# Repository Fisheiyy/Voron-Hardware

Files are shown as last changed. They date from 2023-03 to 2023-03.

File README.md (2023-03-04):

# Voron-Hardware
Cool Hardware designed by the Voron Design group

| Project | Overview |
|---|---|
| Afterburner_Toolhead_PCB | Breakout PCB for the Afterburner toolhead |
| Daylight on a Stick | LED PCB to illuminate your printer |
| Hall_Effect_XY_Endstop | Replacement for mechanical endstop switches with an adjustable magnetic endstop PCB |
| Klipper_Expander | Standalone MCU for use with Klipper with various inputs and outputs |
| Microswitch_Endstop | PCB for mechanical endstop switches |
| Microswitch_Z_Endstop | PCB for mechanical Z endstop switches |
| Nano_Display | Adapts an Arduino Nano to the RepRap standard 2 2x5pin IDC Connectors |
| PT100Stick | PT100 board in StepStick format |
| SKR-Mini_Screen_Adaptor | PCB to connect a 2 2x5 IDC cable screen to an SKR Mini E3 V1.2/2.0 |
| STM32_Mini12864 | A standalone MCU for use with Klipper to drive a FYSETC Mini 12864 Display |
| Stealthburner_Toolhead_PCB | Breakout PCB for the Afterburner toolhead |
| Taco_Raven | 3D Printer controller with 8 integrated stepper drivers for use with Klipper |
| V0-Umbilical | Set of two PCBs for use with the V0.1 to make wiring easier and more modular |
| V0_Display | Small Form Factor Display with OLED, Rotary Encoder or Buttons and Neopixel LED |
| V0_Display_RP2040	 | Derivitive of V0 Display to use RP2040 over STM32 |
| V0_Micro_Display | Micro Form Factor Display with OLED, Clickable D-pad and Neopixel LED |
| V0_PCB_Mod | V0 Mod by JNP |
| V0_Simple_Display | V0 Simple Display is a remix of the V0 Display that doesnt need an STM32 MCU |

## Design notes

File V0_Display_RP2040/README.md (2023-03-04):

# RP2040 V0 Display #
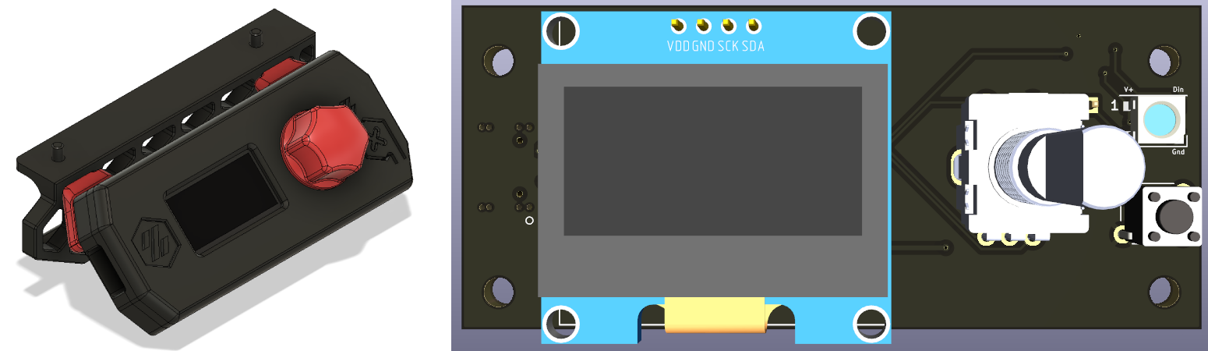
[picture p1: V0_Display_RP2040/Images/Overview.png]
V-Naught_Display


[iBOM](http://htmlpreview.github.io/?https://github.com/Fisheiyy/RP2040_V0_Display/blob/master/KiCad/ibom.html)
### Derived from [Timmit99's V0 Display](https://github.com/VoronDesign/Voron-Hardware/tree/master/V0_Display)
### Sponsored by Provok3d.com & Lab4450.com

## The board has: ##
 - RP2040 MCU with 12MHz Crystal
 - SWD header for easy debugging (not populated by default)
 - USB C port
 - I2C Screen connections for  1.3" display with jumpers on back for slecting which pins (1 or 2) are power and ground
 - EN11-style click encoder support
 - Reset/kill button
 - 3 GPIO pin header
 - 1 on-board Neopixel with data line broken out for expansion

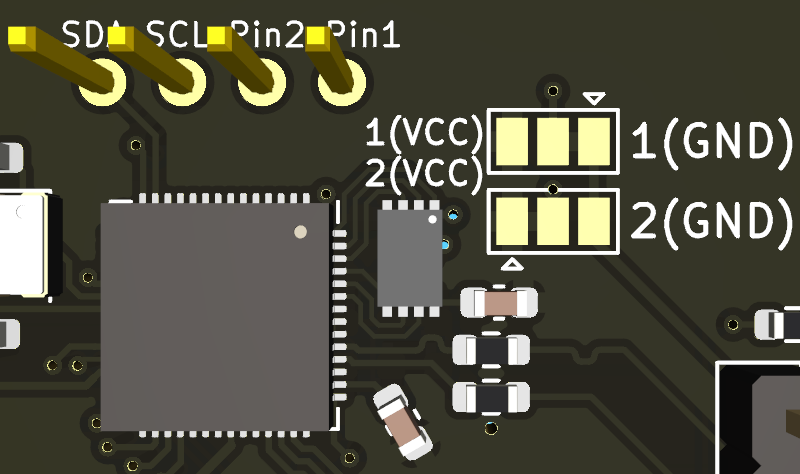
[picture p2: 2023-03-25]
V0_Display_RP2040/Images/I2C_Power_Pin_Selection.PNG

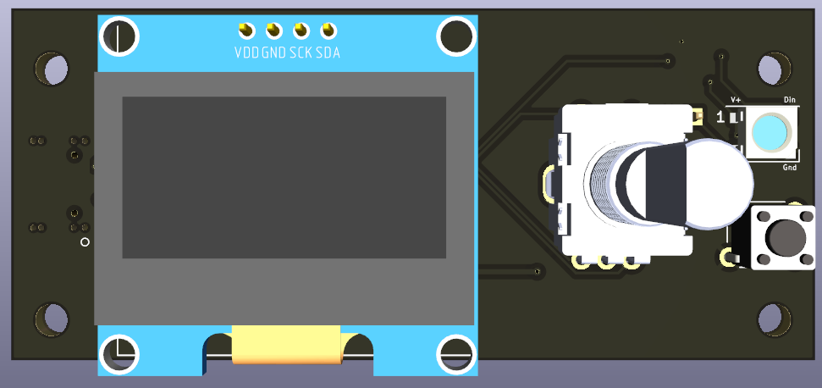
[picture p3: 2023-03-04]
V0_Display_RP2040/Images/Front.png

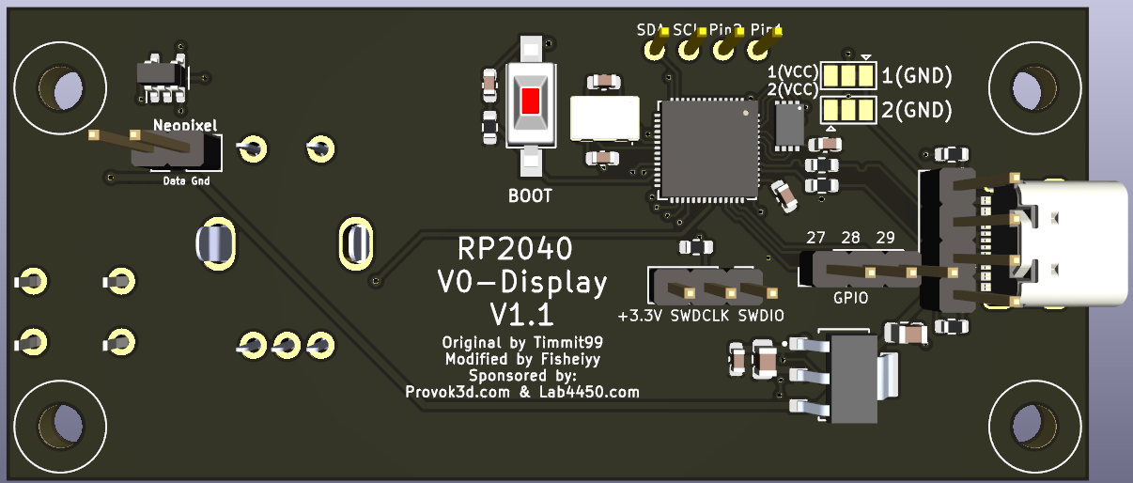
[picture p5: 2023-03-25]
V0_Display_RP2040/Images/Rear.png

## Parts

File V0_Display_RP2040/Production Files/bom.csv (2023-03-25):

Designator | Footprint | Quantity | Value | LCSC Part #
C1, C3 | 0805 | 2 | 22uF | C2859526
C10, C11, C7 | 0603 | 3 | 2.2uF | C71000
C12, C13, C14, C2, C4, C6, C8, C9 | 0603 | 8 | 0.1uF | C30926
C15, C5 | 0603 | 2 | 12pF | C107034
D1 | LED_WS2812B_PLCC4_5.0x5.0mm_P3.2mm | 1 | WS2812B | C2843785
H1, H2, H3, H4 | MountingHole_3.2mm_M3 | 4 | MountingHole
J1 | PinHeader_1x03_P2.54mm_Vertical | 1 | GPIO | C429954
J2 | 1pt3in_OLED | 1 | I2C Header | N/A
J3 | PinHeader_1x03_P2.54mm_Vertical | 1 | SWD | C429954
J4 | USB_C_Receptacle_G-Switch_GT-USB-7010ASV | 1 | GT-USB-7010ASV | C2988369
J5 | PinHeader_1x04_P2.54mm_Vertical | 1 | USB_Header
J6 | PinHeader_1x02_P2.54mm_Vertical | 1 | Neopixel | C2894925
JP1 | SolderJumper-3_P1.3mm_Bridged12_Pad1.0x1.5mm | 1 | Pin2 | N/A
JP2 | SolderJumper-3_P1.3mm_Bridged12_Pad1.0x1.5mm | 1 | Pin1 | N/A
JP3 | SW_SPST_FSMSM | 1 | RUN | C118141
R1, R3, R6, R8 | 0603 | 4 | 10K | C304415
R2 | 0603 | 1 | 1K | C110774
R4, R5 | 0603 | 2 | 27R | C861276
R7 | 0603 | 1 | 200R | C8218
SW1 | SW_PUSH_6mm | 1 | Kill_SW | C455090
SW2 | EN11_Encoder | 1 | Rotary_Enc | N/A
U1 | AMS1117-3.3 | 1 | AMS1117-3.3 | C6186
U2 | W25Q16JVUXIQ | 1 | W25Q16JVUXIQ | C2843335
U3 | SOT-23-5 | 1 | 74LVC1G17 | C6076
U4 | QFN-56-1EP_7x7mm_P0.4mm_EP3.2x3.2mm | 1 | RP2040 | C2040
Y1 | Oscillator_SMD_SeikoEpson_SG8002CE-4Pin_3.2x2.5mm | 1 | 12MHz | C654949

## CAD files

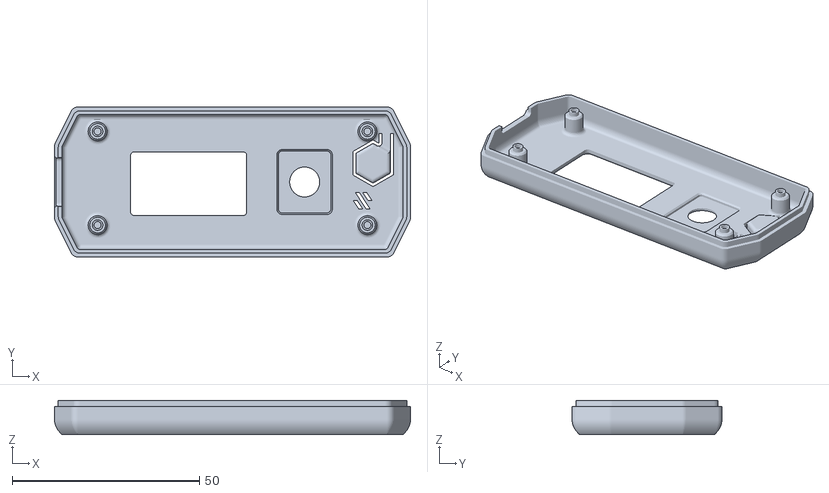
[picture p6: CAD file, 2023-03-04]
V0_Display_RP2040/STLs/Housing_Front_x1.stl
95.0 x 40.0 x 9.10

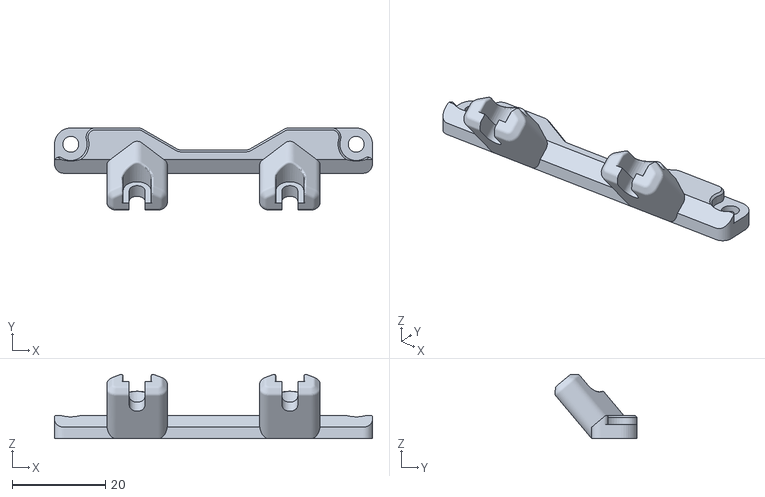
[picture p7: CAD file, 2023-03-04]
V0_Display_RP2040/STLs/V0.1/[a]SinglePieceMount_Slot_x1.STL
68.3 x 17.6 x 13.8

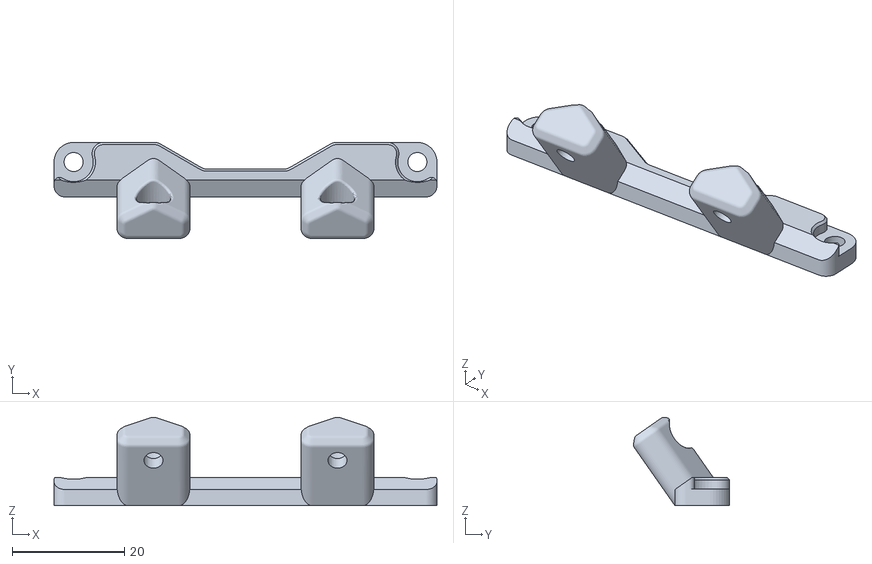
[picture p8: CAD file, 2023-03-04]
V0_Display_RP2040/STLs/V0.1/[a]_Single_Piece_Mount_x1.STL
68.3 x 17.1 x 15.8

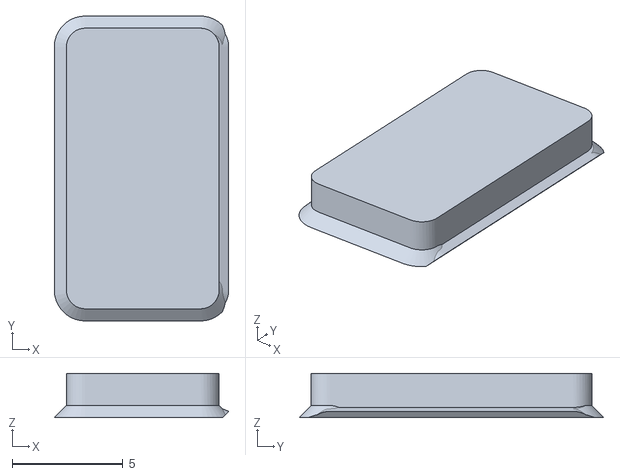
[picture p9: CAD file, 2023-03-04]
V0_Display_RP2040/STLs/USB_Opening_Plug_x1.STL
7.89 x 13.8 x 2.00

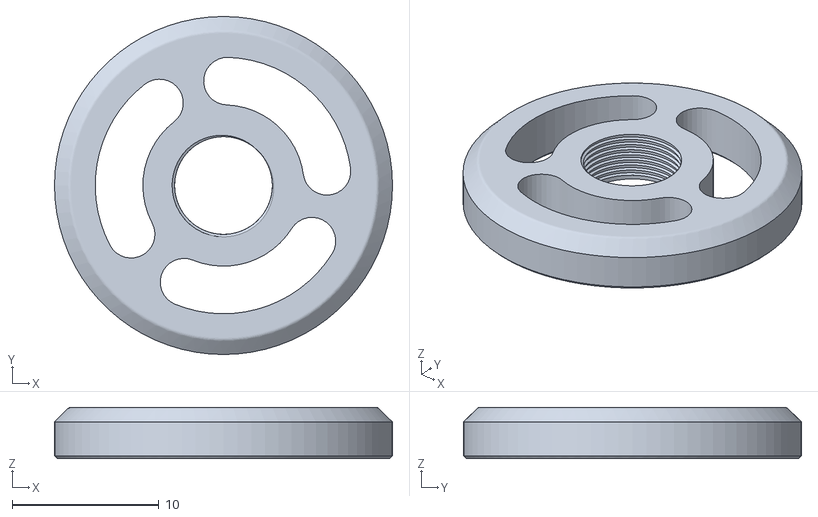
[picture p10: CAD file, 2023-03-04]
V0_Display_RP2040/STLs/[a]_Knob_Spacer_x1.stl
23.0 x 23.0 x 3.50

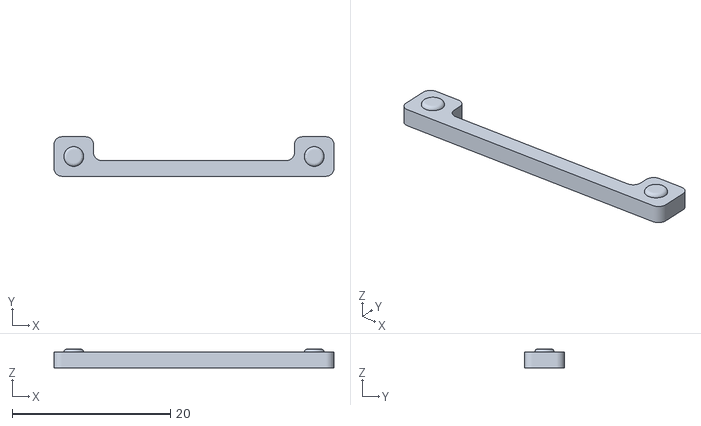
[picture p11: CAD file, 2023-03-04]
V0_Display_RP2040/STLs/Screen_Spacer_x1.stl
35.4 x 5.00 x 2.40

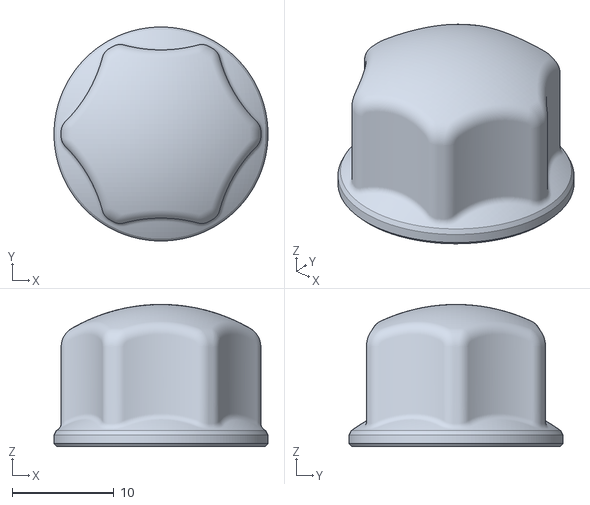
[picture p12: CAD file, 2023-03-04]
V0_Display_RP2040/STLs/[a]_Knob_x1.stl
21.0 x 21.0 x 13.9

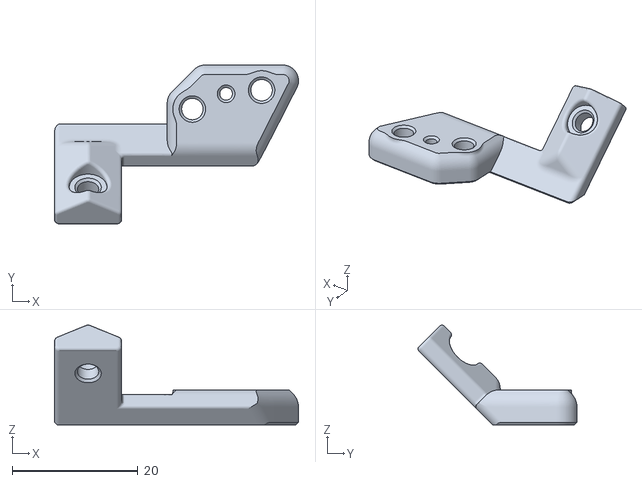
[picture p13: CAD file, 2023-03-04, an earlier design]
V0_Display_RP2040/STLs/V0/[a]_Mounting_leg_x1.stl
38.8 x 25.3 x 15.9

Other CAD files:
V0_Display_RP2040/STLs/Housing_Front_No_USB_x1.stl
V0_Display_RP2040/STLs/V0/[a]_Mounting_leg_mirror_x1.stl

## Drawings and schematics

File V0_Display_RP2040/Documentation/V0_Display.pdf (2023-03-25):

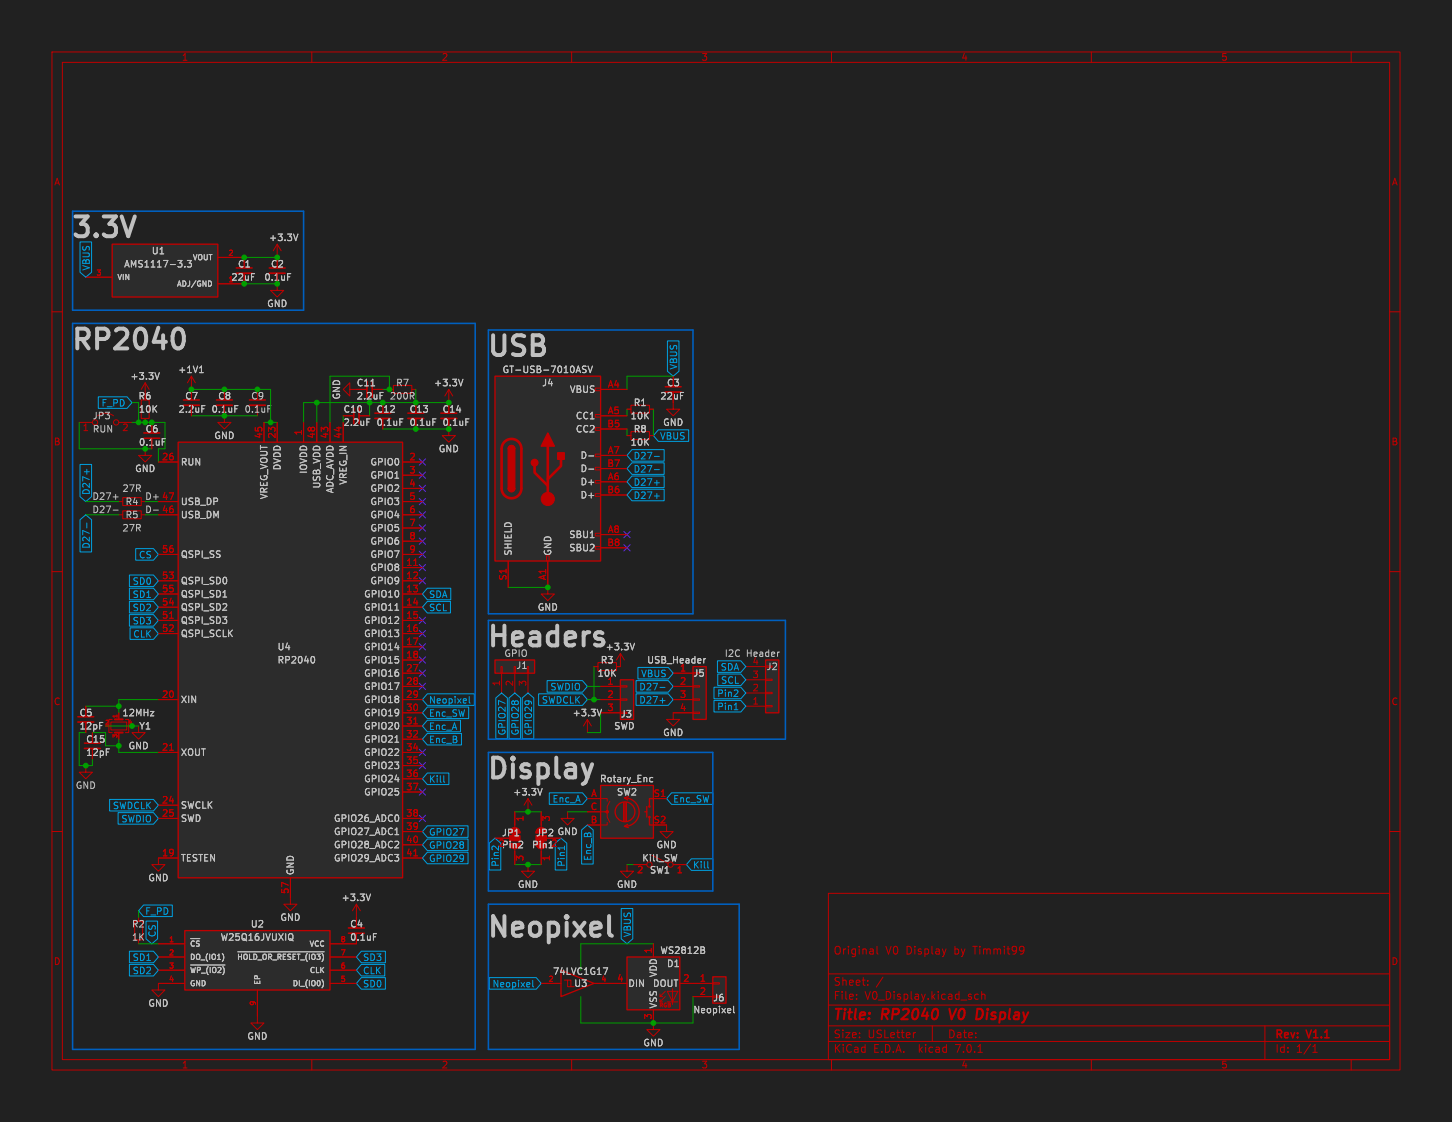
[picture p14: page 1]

D1 WS2812B VDD 1 DOUT 2 VSS 3 DIN 4

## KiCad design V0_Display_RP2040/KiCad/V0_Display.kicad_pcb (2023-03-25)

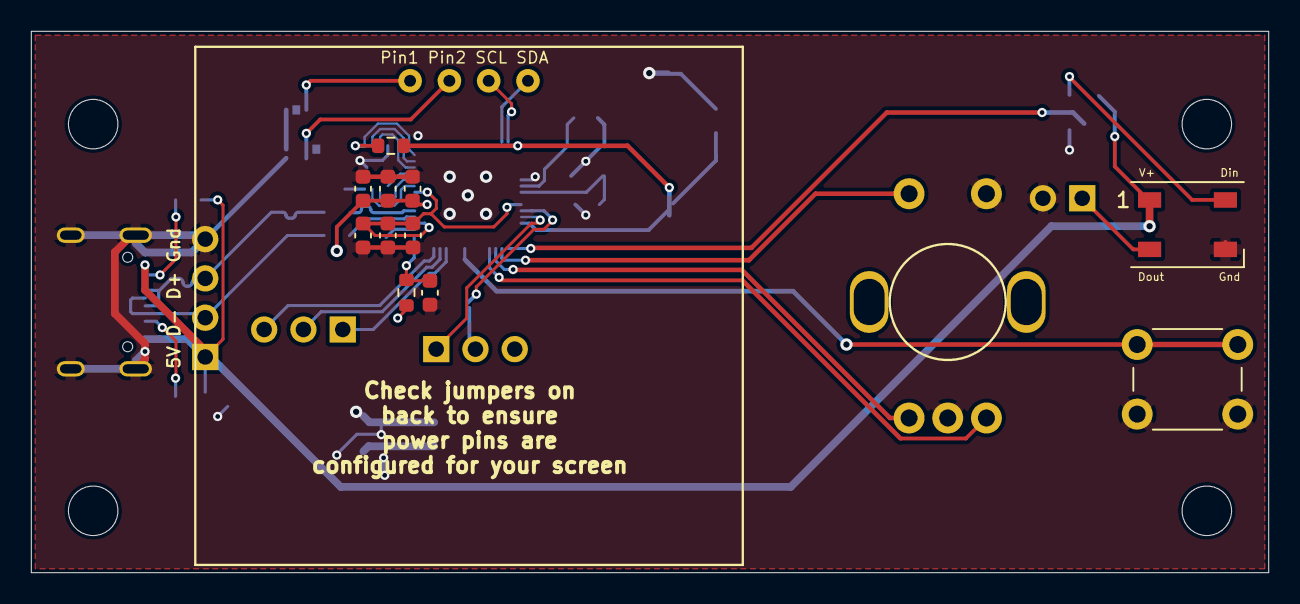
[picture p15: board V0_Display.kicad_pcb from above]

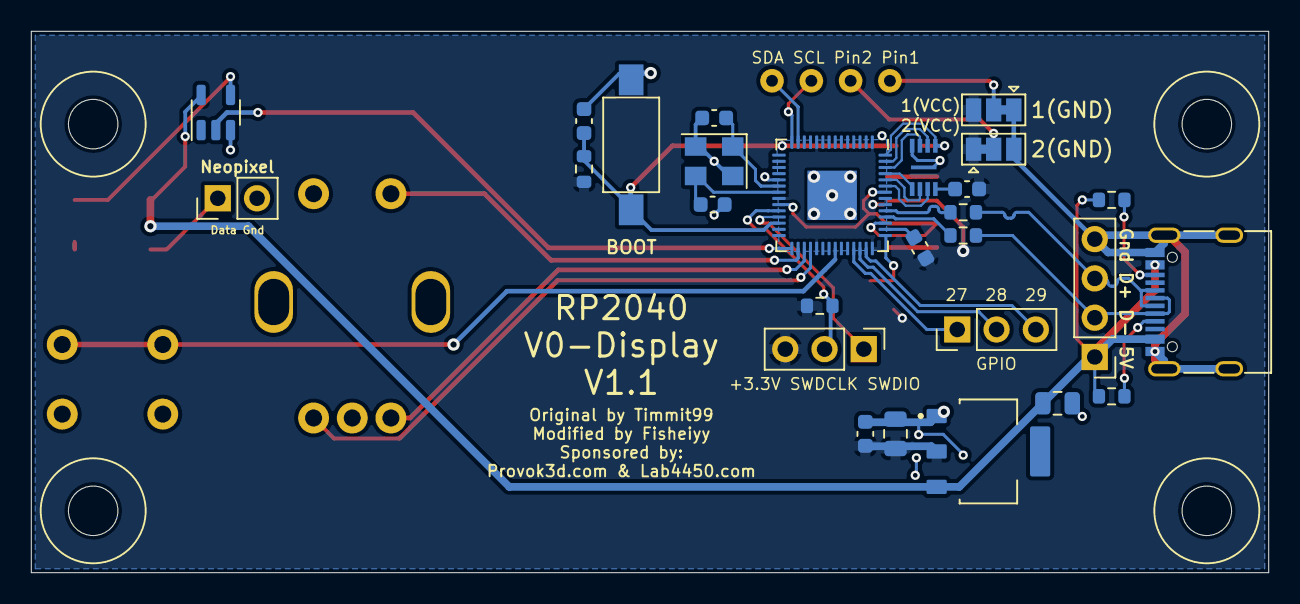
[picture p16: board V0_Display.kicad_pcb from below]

Board: 2 copper layers, 80.0 x 35.0 mm, 44 parts (27 on the bottom side), 38 nets.

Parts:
C1, C3: 22uF; C_0805_2012Metric
C2, C4, C6, C8, C9, C12, C13, C14: 0.1uF; C_0603_1608Metric
C5, C15: 12pF; C_0603_1608Metric
C7, C10, C11: 2.2uF; C_0603_1608Metric
D1: WS2812B; LED_WS2812B_PLCC4_5.0x5.0mm_P3.2mm
H1, H2, H3, H4: MountingHole; MountingHole_3.2mm_M3
J1: GPIO; PinHeader_1x03_P2.54mm_Vertical
J2: I2C Header; 1pt3in_OLED
J3: SWD; PinHeader_1x03_P2.54mm_Vertical
J4: GT-USB-7010ASV; USB_C_Receptacle_G-Switch_GT-USB-7010ASV
J5: USB_Header; PinHeader_1x04_P2.54mm_Vertical
J6: Neopixel; PinHeader_1x02_P2.54mm_Vertical
JP1: Pin2; SolderJumper-3_P1.3mm_Bridged12_Pad1.0x1.5mm
JP2: Pin1; SolderJumper-3_P1.3mm_Bridged12_Pad1.0x1.5mm
JP3: RUN; SW_SPST_FSMSM
R1, R3, R6, R8: 10K; R_0603_1608Metric
R2: 1K; R_0603_1608Metric
R4, R5: 27R; R_0603_1608Metric
R7: 200R; R_0603_1608Metric
SW1: Kill_SW; SW_PUSH_6mm
SW2: Rotary_Enc; EN11_Encoder
U1: AMS1117-3.3
U2: W25Q16JVUXIQ
U3: 74LVC1G17; SOT-23-5
U4: RP2040; QFN-56-1EP_7x7mm_P0.4mm_EP3.2x3.2mm
Y1: 12MHz; Oscillator_SMD_SeikoEpson_SG8002CE-4Pin_3.2x2.5mm

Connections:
+1V1: C7.1, C8.1, C9.1, U4.23 (DVDD), U4.45 (VREG_VOUT), U4.50 (DVDD)
+3.3V: C1.1, C2.1, C4.2, C10.1, C12.1, C13.1, C14.1, J3.3, JP1.1 (A), JP2.3 (B), R3.2, R6.2, R7.2, U1.2 (VOUT), U4.1 (IOVDD), U4.10 (IOVDD), U4.22 (IOVDD), U4.33 (IOVDD), U4.42 (IOVDD), U4.48 (USB_VDD), U4.49 (IOVDD)
/D+: R4.2, U4.47 (USB_DP)
/D-: R5.1, U4.46 (USB_DM)
CLK: U2.6 (CLK), U4.52 (QSPI_SCLK)
CS: R2.1, U2.1 (~CS), U4.56 (QSPI_SS)
D27+: J4.A6 (D+), J4.B6 (D+), J5.3, R4.1
D27-: J4.A7 (D-), J4.B7 (D-), J5.2, R5.2
Enc_A: SW2.A, U4.31 (GPIO20)
Enc_B: SW2.B, U4.32 (GPIO21)
Enc_SW: SW2.S1, U4.30 (GPIO19)
F_PD: C6.2, JP3.2 (B), R2.2, R6.1, U4.26 (RUN)
GND: C1.2, C2.2, C3.2, C5.2, C6.1, C7.2, C8.2, C9.2, C11.2, C12.2, C13.2, C14.2, C15.2, D1.3 (VSS), J4.A1 (GND), J4.A12 (GND), J4.B1 (GND), J4.B12 (GND), J4.S1 (SHIELD), J5.4, J6.2, JP1.3 (B), JP2.1 (A), JP3.1 (A), SW1.2 (B), SW2.C, SW2.S2, U1.1 (ADJ/GND), U2.4 (GND), U2.9 (EP), U3.3 (GND), U4.19 (TESTEN), U4.57 (GND), Y1.2, Y1.4
GPIO27: J1.1, U4.39 (GPIO27_ADC1)
GPIO28: J1.2, U4.40 (GPIO28_ADC2)
GPIO29: J1.3, U4.41 (GPIO29_ADC3)
Kill: SW1.1 (A), U4.36 (GPIO24)
Neopixel: U3.2, U4.29 (GPIO18)
unnamed: D1.4 (DIN), U3.4
unnamed: D1.2 (DOUT), J6.1
unnamed: J4.A5 (CC1), R1.1
unnamed: J4.B5 (CC2), R8.1
unnamed: C4.1, U2.8 (VCC)
unnamed: C11.1, R7.1, U4.43 (ADC_AVDD)
unnamed: C10.2, U4.44 (VREG_IN)
unnamed: C5.1, U4.20 (XIN), Y1.1
unnamed: C15.1, U4.21 (XOUT), Y1.3
Pin1: J2.1, JP2.2 (C)
Pin2: J2.2, JP1.2 (C)
SCL: J2.3, U4.14 (GPIO11)
SD0: U2.5 (DI_(IO0)), U4.53 (QSPI_SD0)
SD1: U2.2 (DO_(IO1)), U4.55 (QSPI_SD1)
SD2: U2.3 (~WP_(IO2)), U4.54 (QSPI_SD2)
SD3: U2.7 (~HOLD_OR_RESET_(IO3)), U4.51 (QSPI_SD3)
SDA: J2.4, U4.13 (GPIO10)
SWDCLK: J3.2, R3.1, U4.24 (SWCLK)
SWDIO: J3.1, U4.25 (SWD)
VBUS: C3.1, D1.1 (VDD), J4.A4 (VBUS), J4.A9 (VBUS), J4.B4 (VBUS), J4.B9 (VBUS), J5.1, R1.2, R8.2, U1.3 (VIN), U3.5 (VCC)

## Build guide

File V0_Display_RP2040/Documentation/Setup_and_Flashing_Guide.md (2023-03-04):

## V0 Display Flashing Instructions:

1) Connect to your host raspberry pi via SSH

2) This step depends on if your board has firmware on it or not already:

	a) If you have a pre-flashed board:
		- Connect the board to the host Raspberry Pi via USB
		- Jump to step 9
	
	b) If you have an unflashed board:
		- Hold the BOOT button **while** connecting to your Pi via USB

3) Run `lsusb` from the command prompt
	- Make sure you see a `Raspberry Pi RP2 Boot`
	
4) Run `cd ~/klipper` from the command line to enter the Klipper directory

5) Run `make menuconfig` settings should be:

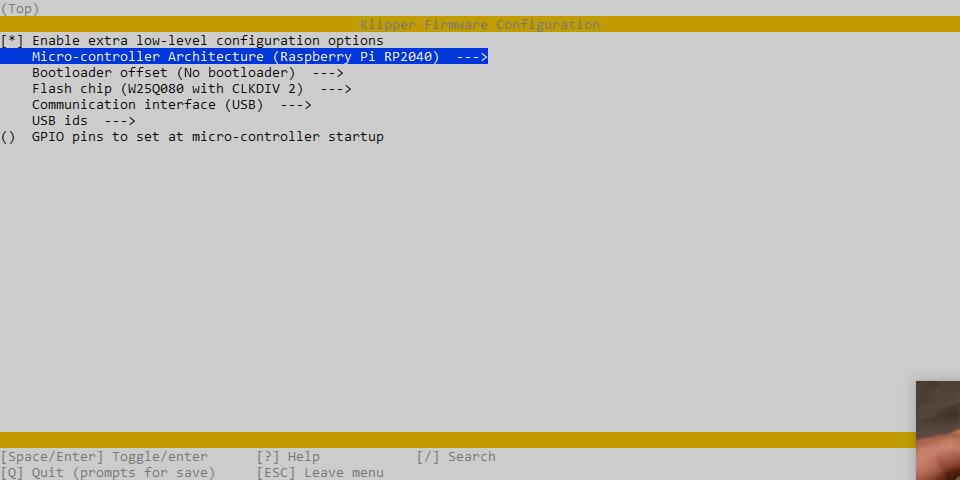
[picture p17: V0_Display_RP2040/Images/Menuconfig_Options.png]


	Exit and Save

6) Run `make clean` to clean up the make environment.

7) Run `make flash FLASH_DEVICE=2e8a:0003`

8) Remove the BOOT jumper

9) Now `ls /dev/serial/by-id/*` should return a device begining with `/dev/serial/by-id/usb-Klipper_rp2040...` 

10) Copy this serial port name (`/dev/serial/by-id/usb-Klipper_rp2040...` )and place it in your [mcu display] section of the display config file.

Your board should now be usable with Klipper. Use the example config file to get started
Best option is to copy the config file into the same directory as `printer.cfg` then add `[include V0Display.cfg]` to the end of your `printer.cfg` to include the file.

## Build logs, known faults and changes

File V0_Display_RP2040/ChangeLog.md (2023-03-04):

# Change Log #

## V1:
 - Changed STM32F042 for RP2040
 - Changed SMD Components from 0805 to 0605
 - Changed USB Micro B to USB C
 - Cleaned up Schematic
 - 1 Ground and 1 3.3V Plane

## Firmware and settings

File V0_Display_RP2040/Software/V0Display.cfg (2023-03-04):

[mcu display]
#serial: **PASTE YOUR SERIAL PORT HERE AND UNCOMMENT**
restart_method: command

[display]
lcd_type: sh1106
i2c_mcu: display
i2c_bus: i2c1
# Set the direction of the encoder wheel
#   Standard: Right (clockwise) scrolls down or increases values. Left (counter-clockwise scrolls up or decreases values.
encoder_pins: ^display:gpio5, ^display:gpio6
#   Reversed: Right (clockwise) scrolls up or decreases values. Left (counter-clockwise scrolls down or increases values.
#encoder_pins: ^display:gpio6, ^display:gpio5
click_pin: ^!display:gpio7
kill_pin: ^!display:gpio8
#x_offset: 2
#   Use X offset to shift the display towards the right. Value can be 0 to 3
#vcomh: 0
#   Set the Vcomh value on SSD1306/SH1106 displays. This value is
#   associated with a "smearing" effect on some OLED displays. The
#   value may range from 0 to 63. Default is 0.
#   Adjust this value if you get some vertical stripes on your display. (31 seems to be a good value)

[neopixel displayStatus]
pin: display:gpio9
chain_count: 1
color_order: GRB
initial_RED: 0.2
initial_GREEN: 0.05
initial_BLUE: 0

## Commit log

2023-03-04 Add V0_Display_RP2040
    [Housing_Front_No_USB_x1.stl, Housing_Front_x1.stl, Screen_Spacer_x1.stl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]
2023-03-05 Fix Footprints
    [V0_Display-B_Cu.gbr, V0_Display-B_Mask.gbr, V0_Display-B_Paste.gbr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]
2023-03-22 Update Files
    New 3.3V Regulator
    "Fixed" Neopixel Level Shifter
    [V0_Display-B_Cu.gbr, V0_Display-B_Mask.gbr, V0_Display-B_Paste.gbr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]
2023-03-25 Rev 1.1
    Fix Vreg-Out Problem
    Change to AMS1117-3.3
    22uF Input Capacitor on VBUS (5V IN)
    [V0_Display-B_Cu.gbr, V0_Display-B_Mask.gbr, V0_Display-B_Paste.gbr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]
